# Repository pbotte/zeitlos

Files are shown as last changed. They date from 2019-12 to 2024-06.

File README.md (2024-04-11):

# Ladensystem für einen automatischen Dorfladen

Ein Paket aus Soft- und Hardware für ein automatisches Ladensystem, welches sich für kleine Läden, bis ca. 1000 Produkte, eignet. Das System basiert darauf, dass jedes Produkt durch eine eigene Waage gewogen wird, welche mit einem Computer verbunden ist.

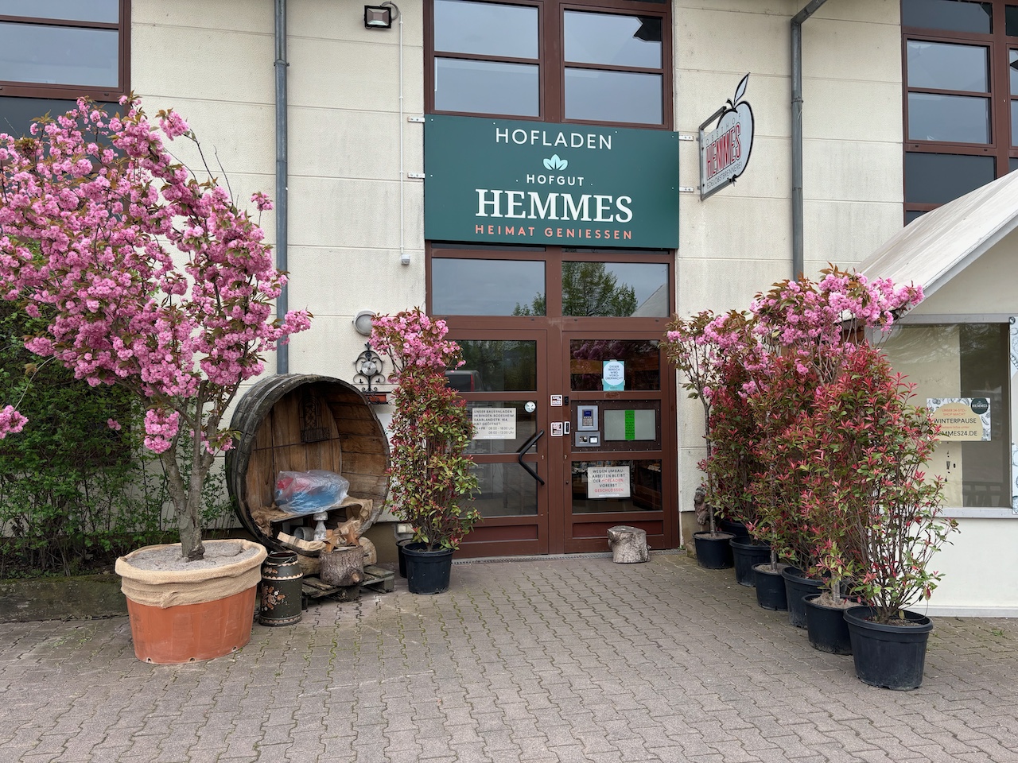
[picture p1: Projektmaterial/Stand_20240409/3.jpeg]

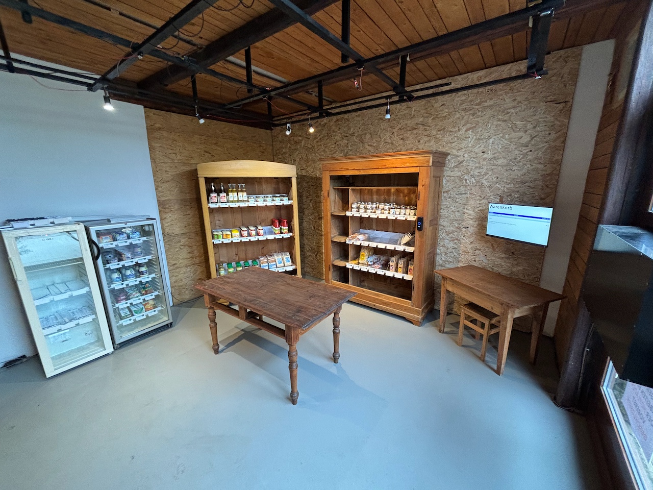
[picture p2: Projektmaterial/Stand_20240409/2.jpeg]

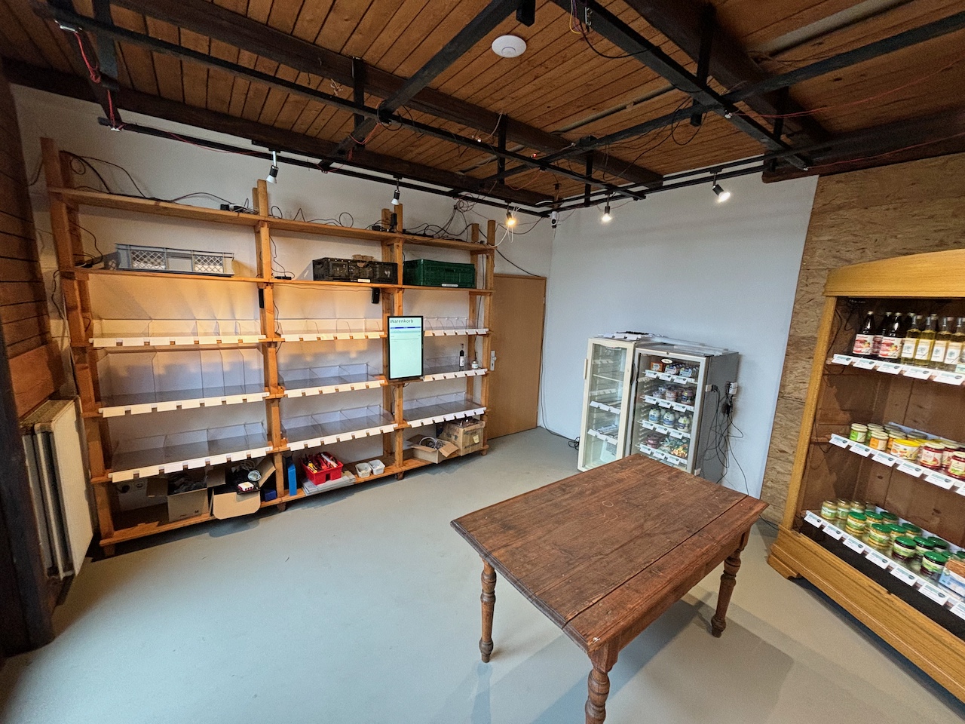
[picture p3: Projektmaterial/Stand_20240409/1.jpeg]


## Beschreibung eines typischen Einkaufs:
1. Einlass mit Girocard oder Kreditkarte. Dabei findet eine Vorauthorisierung (Reservierung von Geld) statt.
2. Der Kunde betritt den Laden und entnimmt die Waren selbst aus den Regalen. Die Anzeige der entnommen Waren und Massen erfolgt sofort und automatisch auf den Kundendisplays.
3. Zum Abschluss des Einkaufs verlässt der Kunde den Laden. Die Abrechnung erfolgt anschließend automatisch über die Karte ohne dass die Karte erneut vorgezeigt werden muss.

Es kann immer nur ein Kunde gleichzeitig einkaufen.

## Hinweise
* [Kostenübersicht](kostenuebersicht.md)

## Technische Details 
* [Zustände eines Einkaufs](ablauf.md)
* [Bestandteile des Ladens / MQTT-Übersicht](MQTT_Overview.md)
* In den jeweiligen Unterordnern gibt es weitere Markdown-Dateien mit Erläuterungen zur Installation und Befehlen.
* Zum gleichzeitigen Herunterladen der Submodule: 
  ```bash
  git clone --recurse-submodules  git@github.com:pbotte/zeitlos.git
  ```

## Lizenz
Alle Soft- und Hardware stehen unter der [GPL v3](https://github.com/pbotte/zeitlos/blob/master/LICENSE) zur freien Verfügung.

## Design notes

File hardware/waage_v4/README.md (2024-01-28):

# Waage V4

* Waage aus 3D Drucker
* Wiegen mit 4 Wägezellen, Halbbrücke
* Kosten: 25€/Waage mit Druck und Elektornik, ohne Montage.
* Stand: Fertig entwickelt.

## 3D-Daten: 

[Modell hier herunterladen](https://cad.onshape.com/documents/e93dca015aaa1e9e19b301b1/w/7b48b7bfd47193fa3707ac4f/e/e2c3e895b10e82bbda4e5613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
) und ausdrucken via
* 3D FDM Drucker, oder
* https://craftcloud3d.com

## Elektronik-Platine:
* [Schematics](elektronik/illustrative/schematics.pdf)

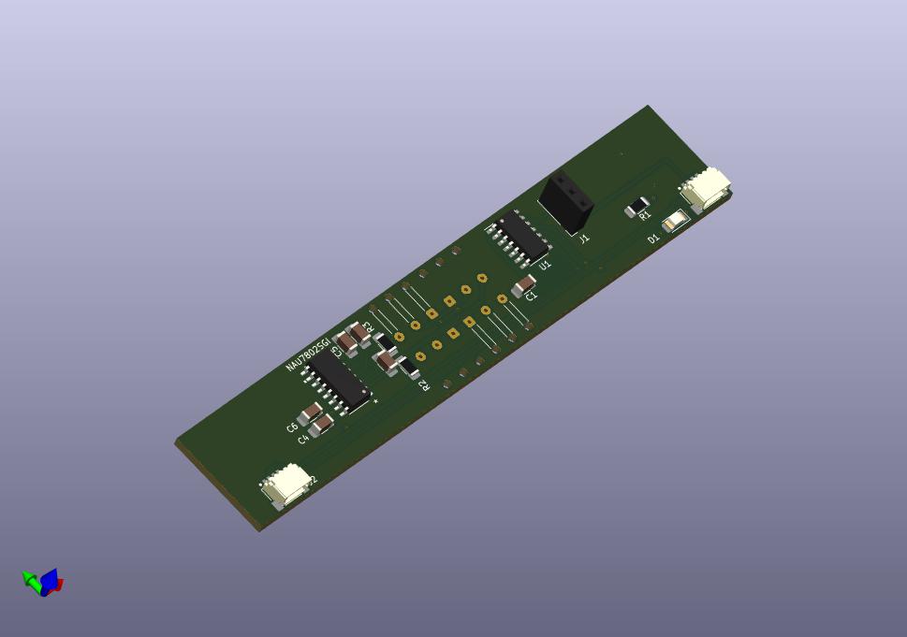
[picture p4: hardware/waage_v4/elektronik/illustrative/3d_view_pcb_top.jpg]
Top

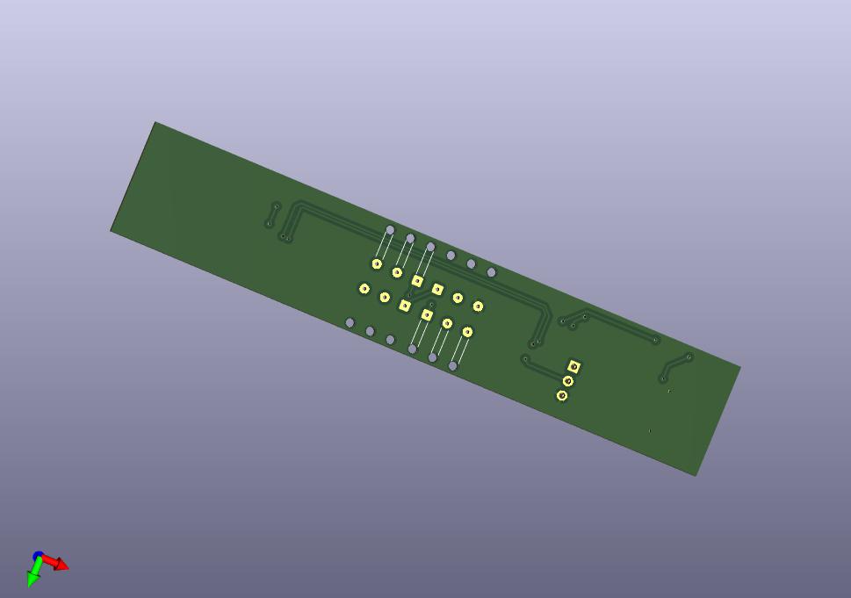
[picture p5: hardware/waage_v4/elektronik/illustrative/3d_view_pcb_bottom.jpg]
Bottom


## Materialien:
* Anschlusskabel: 
  * 50mm
  * https://www.mouser.de/ProductDetail/485-4399
* 4er Set Wägezellen:
  * Halbbrücken
  * 40cm Kabel
  * 1kOhm
  * https://www.aliexpress.com/item/1005004455387340.html
* Acrylglas Rundstab 2mm
  * klar, als Lichtleiter eingesetzt
  * https://hbholzmaus.de/epages/Store7_Shop34800.sf/de_DE/?ObjectPath=/Shops/Shop34800/Products/%2200-Ø2-00%22/SubProducts/%2200-Ø2-2000%22

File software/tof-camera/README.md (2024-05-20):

# Ausführung

```bash
pip install --break-system-packages -r requirements.txt

python3 ./software/roy-tof-camera/libroyale-5.10.0.2751-LINUX-arm-64Bit/python/tof_camera_readout.py -v -b 192.168.10.10
```

# Vobereitung

### Hardware:
- Raspi 4B, 1GB
- Raspbian, 64bit, Desktop

### Erster Test, ob Kamera korrekt angeschlossen:

```bash
cd Desktop/libroyale-5.10.0.2751-LINUX-arm-64Bit/bin/
sudo ./royaleviewer 
```

### udev-rules installieren, damit ohne sudo ausführbar
```bash
cd Desktop/libroyale-5.10.0.2751-LINUX-arm-64Bit/driver/udev/
sudo cp 10-royale-ubuntu.rules /etc/udev/rules.d/
```

### System vorbereiten
Anleitung: https://www.youtube.com/watch?v=8IJLDIYbaCg&t=156s
```bash
cd Desktop/libroyale-5.10.0.2751-LINUX-arm-64Bit/python/
sudo apt update
sudo apt upgrade
sudo apt install libusb-1.0-0 qtbase5-dev libopengl0 python3 python3-tk python3-matplotlib python3-numpy cmake cmake-gui swig
sudo reboot
````

Warpper für aktuelles python installieren
```bash
cd Desktop/libroyale-5.10.0.2751-LINUX-arm-64Bit/python/
cat README.md 

#noch eine Datei reinkopieren:
# von hier: https://github.com/numpy/numpy/tree/master/tools/swig
cd swig
wget https://raw.githubusercontent.com/numpy/numpy/main/tools/swig/numpy.i

#cmake-gui braucht das aktuelle Verzeichnis der libpython, dies ggf. mit find zuvor suchen
PYTHON_LIBRARY=/usr/lib/aarch64-linux-gnu/libpython3.11.so cmake-gui 

#Vorgehen / dort auswählen:
# - Eingabe-Pfad: python/swig Verzeichnis
# - Ausgabe neuen Ordner: python/build
# Configure, dort 2. Eintrag in Dropdown auswählen: "UNIX..."
# Haken bei cmake option für numpy.i anwählen
# Generate klicken
# cmake-gui verlassen

#build script ausführen
cd python/build/
make

#erzeugte Datei nach python kopieren
cd python/
mv _roypy.so _roypy.so-3.8
cp build/_roypy.so .
```
### Beispiel ausprobieren
```bash
python3 ./sample_retrieve_data.py 
````

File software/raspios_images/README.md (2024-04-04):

# Installation eines Computers

## Quick and easy:

1) Use [Raspberry Pi Imager](https://www.raspberrypi.com/software/), copy lite or standard image to SD card. Activate SSH server, set hostname (eg `shelf01`) and password for user `pi`. Check the right localisation options. Press `CTRL + SHIFT + X` in the imager to reach the advanced options.

   ALTERNATIVELY: Hold down the `shift`-key while powering up the raspberry and install the OS with the right custom settings.
2) After the first boot, run: 
   ```bash
   curl -fsSL https://raw.githubusercontent.com/pbotte/zeitlos/master/software/get.sh -o get.sh
   sudo bash get.sh
   ```
Done.

If you prefere the long way, choose this:

## The long way

Alle Opterationen in dem Verzeichnis
```bash
cd raspi_image
```

### Download des Images

Wir laden für alle Desktops to Version mit Desktop von der [offiziellen Seite](https://www.raspberrypi.com/software/operating-systems/), um später leichter einen Browser anzeigen zu können. Später wird lediglich entschieden, bis wohin gebootet werden soll (Console oder Desktop)

```bash
wget https://downloads.raspberrypi.com/raspios_armhf/images/raspios_armhf-2023-12-06/2023-12-05-raspios-bookworm-armhf.img.xz
```

### Image und Dateien kopieren

Nachschauen, wo es hingehen soll
```bash
lsblk
#macos
diskutil list
```

Dann kopieren:
```bash
xzcat 2023-12-11-raspios-bookworm-armhf-lite.img.xz | sudo dd of=/dev/sdc bs=1M status=progress conv=fsync

# unter macos 
# use devices with additional "r" eg /dev/rdisk2)
diskutil unmountDisk /dev/disk2
xzcat 2023-12-05-raspios-bookworm-armhf.img.xz | sudo dd of=/dev/rdisk2 bs=1m status=progress conv=sync
```

Alternativ mit separatem Decompress, falls es nicht funktioniert (Das Schreiben hört hie auf...)
```bash
xz -d -v 2023-12-05-raspios-bookworm-armhf.img.xz 
sudo dd if=2023-12-05-raspios-bookworm-armhf.img of=/dev/rdisk2 bs=1m status=progress conv=sync
```

Vorbereiten für das Kopieren der Konfigurationsdateien:
```bash 
mount /dev/sdc1 boot/ 
cp firstrun.sh ./boot/ # macos: Volumes/bootfs 

#entweder die komplette Datei kopieren oder die wichtigen Zeichen in cmdline.txt einfügen
cp cmdline.txt ./boot/ # macos: Volumes/bootfs 
```

Die wichtigen Zeichen in `cmdline.txt` sind:
```
systemd.run=/boot/firstrun.sh systemd.run_success_action=reboot systemd.unit=kernel-command-line.target
```
(Alles in einer Zeile!)

Für Lite-OS in Gänze:
```bash
console=serial0,115200 console=tty1 root=PARTUUID=57c84f67-02 rootfstype=ext4 fsck.repair=yes rootwait quiet init=/usr/lib/raspberrypi-sys-mods/firstboot systemd.run=/boot/firstrun.sh systemd.run_success_action=reboot systemd.unit=kernel-command-line.target ipv6.disable=1
```

### Browser Kiosk Modus

#### Neu, Seit Wayland, ca. 2024

Anleitung: https://www.raspberrypi.com/tutorials/how-to-use-a-raspberry-pi-in-kiosk-mode/

Zusammengefasst: `wtype` installieren und die Datei `wayfire.ini` ergänzen. Im Text den `hostname` anpassen.
```bash
sudo apt install wtype
sudo nano .config/wayfire.ini

[autostart]
panel = wfrespawn wf-panel-pi
background = wfrespawn pcmanfm --desktop --profile LXDE-pi
xdg-autostart = lxsession-xdg-autostart
chromium = chromium-browser http://shop-master/?hostname=shop-display02 --kiosk --noerrdialogs --disable-infobars --no-first-run --ozone-platform=wayland --enable-features=OverlayScrollbar --start-maximized
screensaver = false
dpms = false
```

### Auswerfen 
```bash 
umount ./boot/
#unter mac os
sudo diskutil eject /dev/rdisk2
```

### Hinweise

#### Hinweis 1
Nicht alles was mit raspi-config geht ist [offiziell](https://www.raspberrypi.com/documentation/computers/configuration.html#list-of-options30) dokumentiert. Alternativ den Quellcode nach Befehlen suchen mit:
```bash
curl -sL https://github.com/RPi-Distro/raspi-config/raw/master/raspi-config | grep -E '(do|get)_[a-zA-Z0-9_ ]+\(' | sort | uniq
```
(Tipps von [hier](https://raspberrypi.stackexchange.com/questions/28907/how-could-one-automate-the-raspbian-raspi-config-setup))

#### Hinweis 2

Ein Skript, welches per `systemd.run=/boot/firstrun.sh` (?) gestartet ist, kann nicht auf das Netzwerk zugreifen. Kann man machen, was man will (inkl. Workaround):

https://unix.stackexchange.com/questions/686612/wait-for-network-on-systemd-run-kernel-parameter-like-require-wants-in-systemd

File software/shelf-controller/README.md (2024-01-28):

# Shelf Controller I2C

- MQTT-Client name: `shelf01`, etc.
- MQTT-topic-prefix: `homie/shelf01`
- MAC-Adresse von Scale (6x byte): `aabbccddeeff`
- EEPROM Adressnuztung: 0: I2C Adresse, 1..4: Steigung (4bytes float), 5..8: Nullwert (4bytes float)

| R/W | MQTT Topic <br> (ohne Topic-prefix) | Retain | Typischer Wert | Aktion |
| --- | --- |:---:| --- | --- |
| W | `/state` | X | `0` oder `1` | online / offline, per Last-Will gesetzt |
| R | `/cmd/search` | | | Erneut nach Waagen suchen |
| R | `/cmd/leds` | | `0`oder `1` | Setze alle LEDs am Bus an/aus |
| R | `/cmd/restart` | | egal | Starte alle Waagen am Bus neu. Warte 8 Sekunden, bis dies sicher durchgeführt ist. |
| R | `/cmd/set_zero` | | egal | Setze den aktuellen Mittelwert als `scale_calibration_zero_in_raw` |
| R | `/cmd/scales/aabbccddeeff/set_slope` | | `0.001`..`200` (in kg) | Setze die Steiung zur Kalibration. (Messwert-`scale_calibration_zero_in_raw`)*Steigung = Wert in kg |
| R | `/cmd/scales/aabbccddeeff/led` |  | `0` oder `1` | Schalte individuelle LED ein/aus |
| W | `/scales/aabbccddeeff/state` | X | `0` oder `1` | online / offline (sollte jedoch `/state==0` sein, dann gelten diese Werte nur als historisch) |
| W | `/scales/aabbccddeeff`<br>`/firmware_version` | X | `uint`  | Wird von der Waage ausgelesen |
| W | `/scales/aabbccddeeff`<br>`/hardware_version` | X | `uint`  | Wird von der Waage ausgelesen |
| W | `/scales/aabbccddeeff`<br>`/scale_calibration_zero_in_raw` | X | `32-bit uint`  | Waagen-Kalibration Roh-ADC-Wert bei 0kg auf Waage |
| W | `/scales/aabbccddeeff`<br>`/scale_calibration_slope` | X | `double` | Waagen-Kalibration, Steigung nach Abzug des Roh-0kg-Werts, Ergebnis: kg |
| W | `/scales/aabbccddeeff`<br>`/i2c_address` | X | `9..117` (byte)  | I2C-Adresse der Waage, nur zur Info |
| W | `/scales/aabbccddeeff`<br>`/raw` | | `32-bit uint` | Roh-Messwert des ADCs (nur im Modus `-vv`) |
| W | `/scales/aabbccddeeff`<br>`/mass` | | Wert in kg, double | Aktuelle Masse unter Anwendung der Kalibration ggf. unter Berücksichtigung der Temperatur |
| W | `/scales/aabbccddeeff`<br>`/touched` | | `0`oder `1` | Wenn die Waage zuletzt mit dem Finger belastet wurde ODER eine Laständerung eintrat, dann soll hier eine `1` übermittelt werden. |

## Start von shelf-controller
```mermaid
sequenceDiagram
    actor Techniker
    participant shop-controller
    participant shelf-controller
    participant Waage
    Techniker->>shop-controller: Startet Programm
    shop-controller->>shop-controller: schreibt: shop_overview/products
    shop-controller->>shop-controller: schreibt: shop_overview/products_scales
    Techniker->>shelf-controller: Startet Programm,<br>liest /products und /products_scales<br>(und hält aktuell)
    shelf-controller->>Waage: Sucht nach Waagen
    Waage->>shelf-controller: Meldet sich zurück
    shelf-controller->>Waage: Fragt Waage nach Roh-Wert
    Waage->>shelf-controller: Gibt Roh-ADC-Messwert
    shelf-controller->>shelf-controller: Wendet Kalibrierung von calib/scale-aabbccddeeff an 
```

## Beispiele

| Topic | Wert | 
| --- | --- |
| `homie/shop_controller/shop_overview/products` | `{"1": {"ProductID": 1, "ProductName": "Kuerbis", "ProductDescription": "eigene Ernte", "PriceType": 0, "PricePerUnit": 4.0, "kgPerUnit": 1.67}, "2": {"ProductID": 2, "ProductName": "Nudeln", "ProductDescription": "Hausgemacht mit frischen Eiern", "PriceType": 0, "PricePerUnit": 2.6, "kgPerUnit": 0.5}, "3": {"ProductID": 3, "ProductName": "Cocktailtomaten", "ProductDescription": null, "PriceType": 0, "PricePerUnit": 4.45, "kgPerUnit": 0.5}, "4": {"ProductID": 4, "ProductName": "Tomaten", "ProductDescription": null, "PriceType": 0, "PricePerUnit": 2.15, "kgPerUnit": 0.6}, "5": {"ProductID": 5, "ProductName": "Eier L 10er", "ProductDescription": "aus Bodenhaltung", "PriceType": 0, "PricePerUnit": 3.3, "kgPerUnit": 0.6}, "6": {"ProductID": 6, "ProductName": "Weizenmehl", "ProductDescription": "1kg Type 550", "PriceType": 0, "PricePerUnit": 1.59, "kgPerUnit": 1.04}, "7": {"ProductID": 7, "ProductName": "Gummibaerchen", "ProductDescription": null, "PriceType": 0, "PricePerUnit": 1.9, "kgPerUnit": 0.155}, "8": {"ProductID": 8, "ProductName": "Haltbare Milch", "ProductDescription": "1L im Tetrapack", "PriceType": 0, "PricePerUnit": 1.69, "kgPerUnit": 1.1}, "9": {"ProductID": 9, "ProductName": "Birnen", "ProductDescription": "750g Eigene Ernte Alexander Lukas", "PriceType": 0, "PricePerUnit": 1.0, "kgPerUnit": 0.775}}}` |
| `homie/shop_controller/shop_overview/products_scales` | `{"shelf01/b963": 1, "shelf01/ca44": 2, "shelf01/d660": 5, "shelf01/3320": 6, "shelf01/1a6d": 7, "shelf01/1503": 8, "shelf01/12d4": 12, "shelf01/73d0": 17, "shelf01/95e": 18, "shelf01/2438": 19, "shelf01/84a7": 20, "shelf01/65c0": 21, "shelf01/7b87": 22, "shelf01/7e3e": 23}`

# Automatischer Start und Terminierung des Controllers

Dies geschieht mittels udev und systemd über die beiden Dateien `99-runScales.rules` und `scale@.service`. Durch die Konfiguration in der systemd-Datei ist sichergestellt, dass das Programm erst dann gestartet wird, wenn der serielle Anschluss bereit ist (After=) und beendet wird, sobald dieser verschwindet (BindTo=).

## Installationsanleitung

Nach einem git clone des Repositories müssen die beiden Dateien in die richtigen Systemverzeichnisse kopiert werden:

```bash
sudo cp zeitlos/software/shelf-controller/99-runScales.rules /etc/udev/rules.d/
sudo cp zeitlos/software/shelf-controller/scale@.service /etc/systemd/system/
```
Anschließend noch die Änderungen an Systemd mitteilen mittels:
```bash
sudo systemctl daemon-reload
```
Wird nun ein Scale Controller an den Computer angesteckt, so wird automatisch der Scale Controller gestartet. Wird er entfernt, so beendet sich dieser auch wieder.

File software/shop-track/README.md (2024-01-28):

# Automatischer Start und Terminierung des Controllers

Dies geschieht mittels udev und systemd über die beiden Dateien `99-runShopTrack.rules` und `shop-track@.service`. Durch die Konfiguration in der systemd-Datei ist sichergestellt, dass das Programm erst dann gestartet wird, wenn der serielle Anschluss bereit ist (After=) und beendet wird, sobald dieser verschwindet (BindTo=).

## Installationsanleitung

Nach einem git clone des Repositories müssen die beiden Dateien in die richtigen Systemverzeichnisse kopiert werden:

```bash
sudo cp zeitlos/scaleController/99-runShopTrack.rules /etc/udev/rules.d/
sudo cp zeitlos/scaleController/shop-track@.service /etc/systemd/system/
```
Anschließend noch die Änderungen an Systemd mitteilen mittels:
```bash
sudo systemctl daemon-reload
```
Wird nun ein Raspberry Pico an den Computer angesteckt, so wird automatisch der Shop-Track Controller gestartet. Wird er entfernt, so beendet sich auch der Scale-Track Controller.

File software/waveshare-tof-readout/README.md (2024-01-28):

# Installation Variante 1

Die Datei `shop-track00.service` als Vorlage nehmen und mit dem `/dev/serial/by-path/...` füllen.

```bash
sudo cp shop-track00.service /etc/systemd/system/
```

Dies für jeden angeschlossen Serial-Converter wiederholen und die Ziffern hochzählen.

# Installation Variante 2

## Automatischer Start und Terminierung des Controllers

Dies geschieht mittels udev und systemd über die beiden Dateien `99-runTracker.rules` und `tracker@.service`. Durch die Konfiguration in der systemd-Datei ist sichergestellt, dass das Programm erst dann gestartet wird, wenn der serielle Anschluss bereit ist (After=) und beendet wird, sobald dieser verschwindet (BindTo=).

## Installationsanleitung

Nach einem git clone des Repositories müssen die beiden Dateien in die richtigen Systemverzeichnisse kopiert werden:

```bash
sudo cp zeitlos/software/waveshare-tof-readout/99-runTracker.rules /etc/udev/rules.d/
sudo cp zeitlos/software/waveshare-tof-readout/tracker@.service /etc/systemd/system/
```
Anschließend noch die Änderungen an Systemd mitteilen mittels:
```bash
sudo systemctl daemon-reload
```
Wird nun ein Serial Converter an den Computer angesteckt, so wird automatisch das Prorgamm gestartet. Wird er entfernt, so beendet sich dieses auch wieder.

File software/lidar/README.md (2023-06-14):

# Installationshinweise

## lidar-readout 

Service auf dem Raspi, an dem der Lidar via USB angeschlossen ist, welcher nur die Daten ausliest und 
anschließend per MQTT versendet.

Vor dem Laden Betreten soll immer eine Referenz-Messung durchgeführt werden (Temperatur unterschiede, Wackler bei Anbringung etc., Rumstehende Dinge). 

## lidar-control

Service auf dem zentralen Computer, welcher die Daten von ggf. mehreren lidar-readouts entgegenimmt und 
eine eine zentrale Aussage über die Belegung des Ladens erzeugt. Gibt auch die Befehle über an/aus an
die einzelnen Lidars weiter.

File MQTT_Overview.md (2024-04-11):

```mermaid
graph TD
  W1["Waagen 1..N"] <--> |I2C| WC1
  W2["Waagen 1..N"] <--> |I2C| WC2
  W3["Waagen 1..N"] <--> |I2C| WCN

  WC1["shelf-controller.py 1"] ==> |Messwerte| SC
  WC2["shelf-controller.py 2"] ==> |Messwerte| SC
  WCN["shelf-controller.py N"] ==> |Messwerte| SC

  L1["Lidar 1..4"] --> |Serial| ST1
  L2["Lidar 1..4"] --> |Serial| ST2
  LN["Lidar 1..4"] --> |Serial| STN

  ST1["Lidar Readout 1"] ==> |Rohdaten| STI
  ST2["Lidar Readout 2"] ==> |Rohdaten| STI
  STN["Lidar Readout N"] ==> |Rohdaten| STI

  Türkontakt --> |Klingeldraht| IOR

  SC["Shop controller"]

subgraph Messdaten-Input
  WC1
  WC2
  WCN
  cardreader
  STI["shop-track-collector.py"]
  IOR["io-usb-readout"]
end

subgraph Ausgabe
  FSR["FSR14Control"]
  DPC["display-power-control"]

  MN["mqtt-2-ntfy"]

  Shelly["Shelly Rollladen-Controller"]

  UW["Update Public Webpage"]
end

  SC ==> Shelly --> Rollladen
 
  IOR ==> |offen/zu| SC

  DPC --> CD1
  DPC --> CD2
  DPC --> CDA

  CD1["Client Live Display 1"]
  CD2["Client Live Display 2"]
  CDA["Client Display Außen"]

  FSR --> LI["Licht innen"]
  FSR --> LA["Licht außen"]
  FSR --> Türöffner

  STI ==> |Kunde im Laden?| SC
  cardreader <==> SC

  SC ==> FSR
  SC ==> DPC

  SC ==> MN

  SC ==> UW

  NR["NodeRed"] <==> SC
```

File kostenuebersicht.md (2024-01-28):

# Kostenübersicht

Alle Preise inkl. MwSt. Stand: 9.1.2023

## Präsenzsystem
Zur Bestimmung, ob Personen im Laden vorhanden. Bezählt wird nur die begehbare Ladenfläche ohne Stellfläche für Regale.

Pro m^2 Ladenfläche, je 1x:
- [Waveshare 18301 TOF Laser Entfernungsmesser](https://www.welectron.com/Waveshare-18301-TOF-Laser-Range-Sensor) 25€
- Verbindungskabel 1m, [kundenspezifische Anfertigung Alibaba](https://hshytech.en.alibaba.com/), 1,20€/Stück
- Halterung aus Plastik, 3D-Druck, Materialkosten: 0,25€
- 2 Schrauben M3x8mm
- 2 Holz-Schrauben 3x18

Pro 8m^2 Ladenfläche:
- [Serial to USB-Konverter 3,3V](https://www.berrybase.de/konverter-micro-usb-buchse-uart-pl2303) 3,90€
- USB-Kabel 2€

Falls mehr als 4 USB-Konverter: USB-Hub für 20€

Für die Auslese:
- [Raspberry Pi 4 1GB](https://www.berrybase.de/raspberry-pi-4-computer-modell-b-1gb-ram?c=319) (39,90€)
- [microSD Speicherkarte High Endurance](https://www.berrybase.de/sandisk-high-endurance-microsdhc-uhs-i-u3-speicherkarte-adapter-32gb) 9,30€
- [Raspberry USB-Netzteil](https://www.berrybase.de/offizielles-raspberry-pi-usb-c-netzteil-5-1v/3-0a-eu-schwarz) 7,90€
- [Gehäuse](https://www.berrybase.de/offizielles-gehaeuse-fuer-raspberry-pi-4-schwarz/grau) 4,90€
- [Netzwerkkabel 10m](https://www.berrybase.de/cat-6-netzwerkkabel-s/ftp-ls0h-weiss?number=93503&c=277) 6,50€ 

### Summe
Bei 16m^2: 515€

## Waagen

Pro Waage, 125mm Breite:
- [Alu-Metallplatte mit Laser-Schnitt, 379x122x2,5mm](https://laserteileonline.de/laserteile-konfigurator/): 6,73€
- [4x Wägezelle](https://de.aliexpress.com/item/1005004455387340.html): 2,46€
- Plastikunterteil, ca. 8€
- [Produkttrenner, Rechteckig, 2mm PETG:](https://kunststoffplattenprofis.de/produkt/pet-g-farblos/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): 1,50€
- T-Stück zum Halten des Produkttrenners, 3D-Druck, 0,06€
- Rückwand: (anteilig) 0,74€
- [Metall-Viereckstab vorne](https://alu-spezi.de/epages/39916185-3f40-410c-8304-8e98310e5b8d.sf/de_DE/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): (anteilig) 0,50€
- Preisschild, 3D-Druck: 0,36€
- Elektronik, JLCPCB: 4,50€
- [Qwiic-Verbindungskabel](https://www.mouser.de/ProductDetail/485-4399): 1,05€
- [Acrylglas-Stab für Lichtleiter](https://hbholzmaus.de/epages/Store7_Shop34800.sf/de_DE/?ObjectPath=/Shops/Shop34800/Products/%2200-Ø2-00%22/SubProducts/%2200-Ø2-2000%22): (anteilig) 0,5€

### Summe
26,40€ pro Waage

Bei 200 Waagen: 5280€

Anmerkung: Zusammenbau und Anlöten der Wägezellen fehlt.

## Waagenauslese

Pro Regalebene (1-20 Waagen):
- Ausleseelektronik, JLCPCB: 7€
- QWIIC-Kabel 50cm: 3€
- USB-Kabel: 2€

Pro 7 Auslese-Elektroniken:
- USB-Hub: 20€
- Auslese-Computer: Raspberry Pi, 1GB (+ Zubehör): 62€
- Netzwerkkabel 10m: 6,50€

### Summe

Typisch sind 25 Auslesen, 3 Hubs und 3 Computer: 565 €

## Kundenanzeige

- 24" HDMI-Monitor: 130€
- HDMI-Kabel (HDMI auf Mini-HDMI): 5€
- Raspberry PI mit 2GB (+ SD-Karte, Netzteil, Gehäuse): 72€
- Netzwerkkabel 10m: 6,50€
- Monitorhalterung: 30€

### Summe

Pro Anzeige: 244€

## Kartenlesegerät 

- OPP C60 für 1600€ (plus MwSt.)
- Halterungen, 3D gedruckt, mit Gewindeeinsätzen: 10€

## Überwachungssystem

- Dreammachine Pro: 520€
- Festplatte: 100€
- 3x Kamera G3 flex plus Netzwerkkabel: 80€+10€
- Netzwerkschrank: 80€
- WLAN AP: 100€
- Türklingel G4 WLAN außen: 190€
- Türklingel Ge PoE innen + Türgong: 420€

### Summe
1680€

## Türzugang und Beleuchtungssteuerung

- Elektroschrank mit Türe: 50€
- Raspberry Pi (+ SD-Karte, Netzteil, Gehäuse): 72€
- USB-RS485-Konverter: 15€
- Eltako FSR14-4x: 45€
- Eltako: FBA14: 23€
- Netzteil für Relais, 12V: 30€
- 12V Netzteil für Magnetschalter Türe: 15€
- Magnetschalter Türe: 20€
- Magnet-Türkontakt: 10€
- Kabel: 230V und Steuerkabel Türe

### Summe
280€

## Kontrollrechner

Kontrolliert den ganzen Laden:
- Raspberry 4GB (+ SD-Karte, Gehäuse, Netzteil): 92€
- Netzwerkkabel 1m: 1,50€

## Globale Summe

Für ein System mit 200 Waagen und 16m^2 begehbare Ladenfläche.

| Teilsystem | Kosten in € |
|---| ---:|
| Präsenzsystem für 16m^2 |  515|
| 200x Waagen | 5.280 |
| 25x Waagenauslese | 565 |
| 3x Kundenanzeige | 732 |
| Kartenlesegerät | 1.600 |
| Kameraüberwachung | 1.680 |
| Türzugang und Beleuchtungssteuerung | 280 |
| Kontrollrechner | 93 |
| **Summe** | 10.745  |

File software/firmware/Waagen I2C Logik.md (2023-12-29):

# Waagen I2C 

- Der Master fragt regelmäßig alle Waagen ab, so schnell er kann. 
- Die LED wird bei Bedarf geändert. 
- Master kann einen Busscan durchführen um den Waagen eine neue eindeutige I2C Adresse zu geben.

## Generelle Logik

- Daten in EEPROM:
  - EEPROM, byte 0: I2C-Adresse (7bit)
  - EEPROM, bytes 1..4: 4bytes float Steigung
  - EEPROM, bytes 5..8: 4bytes float Waagen-Nullwert

- Alle Waagen haben eine 6x 8bit MAC-Adresse. Sie wird aus der Chip Seriennummer abgeleitet.

- I2C Bus-Geschwindigkeit: sollte so niedrig sein, dass er auch als "Feldbus" über die langen Distanzen funktionieren kann. 
  - Evtl. die Widerstände niedriger wählen, siehe auch https://www.nxp.com/docs/en/application-note/AN10216.pdf Slide 41 auf Seite 17. 
  - 1,3kOhm ist die statische untere Grenze, daneben gibt es noch eine dynamisch (rise time).

Alle Waagen hören lesend auf:
- Adresse `0x00` (Broadcast/"General Call", https://www.i2c-bus.org/addressing/general-call-address/, nur schreibend möglich, kein Lesen von target)
- schreibend auf `0x08` (erste freie Adresse nach den reservierten Bereich `0..7`) und 
- r/w auf ihrer individuellen Adressen `9..119`:

| I2C Adr. | Richtung | Byte 0 = cmd | Anz. Bytes <br>(excl. cmd byte) | Erläuterung |
| --- | -- | -- | -- | -- |
| `0x00` | w | `0x00` | 0 | Alle Waagen: Neustart  |
| `0x00` | w | `0x01` | 0 | Alle Waagen: Antwort-Bit zurücksetzen |
| `0x00` | w | `0x02` | 7 | I2C-Adresse setzen, MAC(Bytes 1..6), I2C-Adresse(Byte 7)  |
| `0x00` | w | `0x03` | 6 | Setzen der Referenz-MAC-Adresse, vgl. auch Read von Adresse `0x8` |
| `0x00` | w | `0x04` | 0 | LEDs aller Waagen: aus |
| `0x00` | w | `0x05` | 0 | LEDs aller Waagen: ein |
| `0x08` | r | - | 1 | Rückmeldung ob MAC-Adresse kleiner gleich der gesuchten. |
| `9..119` | r | - | <br>4 ODER<br>13 ODER<br>11 ODER<br>1 | Abhängig von Register: vgl. write `0x00`/`0x01`/`0x04`/`0x06` an `9..119`<br>Waagenwert (Byte 0..3) ODER<br>MAC-Adresse (Byte 0..5) und LED-Status (Byte 6) und BUILD_NUMBER (Byte 7..10) und Hardware_Revision (Byte 11..12) ODER <br>Ergebnis des Selbsttests ODER<br>EEPROM data (single byte) from selected address |
| `9..119` | w | `0x00` | 0 | nächtes Lesen enthält Waagen-Wert |
| `9..119` | w | `0x01` | 0 | nächtes Lesen enthält MAC-Adresse und LED-Status und BUILD_NUMBER und Hardware_Rev |
| `9..119` | w | `0x02` | 0 | LED aus |
| `9..119` | w | `0x03` | 0 | LED an |
| `9..119` | w | `0x04` | 0 | Start Chip Self Test (read result in next step) |
| `9..119` | w | `0x05` | 2 | Write to EEPROM. 1st byte = address, 2nd byte = data byte |
| `9..119` | w | `0x06` | 1 | Prepare read from EEPROM. 1st byte = address. After this command, read one byte from `9..119` |

## Einschalten der Waagen

- Beim Einsetzen der Stromversorgung nimmt die Waage die I2C-Adresse, welche sie bereits zuvor hatte, aus dem EEPROM. 
- Dies dient der Vermeidung von fehlenden Adressen bei  einer wackeligen Stromverbindung oder Stcker-Wackelkontakt.

- Stromversorgung des I2C-Bus sollte via MOSFET durch I2C Master steuerbar sein. Alternativ: USB-Hub mit Power Switch functionality.

## Setzen der I2C-Adressen / Suchen von Waagen

1. Master sendet auf Adresse `0x0` und Daten `0x1`: Alle Waagen setzen ihr Antwort-Bit zurück.
2. Master sendet auf Adresse `0x0` und Daten `0x03`+`0xxx xx xx xx xx xx` (7 bytes): MAC-Adresse, welche bei der nächsten Abfrage als Referenz gilt.
3. Master fragt ab, ob es ein Waage mit MAC-Adresse kleiner der Referenz gibt, die noch das Antwort-Bit gesetzt hat: Lesen eines Bytes von Adresse `0x8`.
4. Client antwortet mit 
   - `0xFF`, falls Antwort-Bit nicht mehr gesetzt ODER Adresse ist größer als Referenz
   - `0x00` (dominant bei Übertragung auf I2C-Bus), falls Adresse kleiner gleich Referenz

5. Der Master fährt so lang mit der Suche fort, bis er die MAC-Adresse einer einzelnen Waage herausgefunden hat. (Binäre Suche, suchen nach MAC-Adresse-1)
6. Der Master sendet nun an Adresse `0x0` ein "I2C Adresse setzen"-Kommando (`0x02`) mit der MAC-Adresse und der I2C-Adresse (8 Bytes).
  - Die Waage speichert sie ins EEPROM. 
  - Die Waage setzt bei sich das Antwort-Bit und antwortet damit bei zukündigen Broadcasts nur noch mit `0xFF`
  - Anschließend (`Wire.begin`) oder Neustart via `resetViaSWR()`
7. Die Suche geht so lang weiter (zurück zu Punkt 2) wie bei einem Broadcast mit der Adresse 0xFFFFFFFFFFFF noch mind. eine Waage antwortet.

ToDO: Falls die Mehrheit der Waagen mit 0xFF die eine antwortende Waage mit 0x0 elektrisch überstimmen sollte, dann muss der I2C-Bus kurzzeitig bei manchen Waagen deaktiviert und auf "z" gesetzt werden.

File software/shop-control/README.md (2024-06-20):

# Installationshinweise

Auf dem RasPi muss vor
```bash
pip install mariadb
#ggf nicht die neueste Version installieren, damit es mit den Dingen aus apt funktioniert:
pip install -Iv mariadb==1.0.7 
```

das folgende installiert werden:
```bash
sudo apt install libmariadb3 libmariadb-dev
```

## QR-Secret-Str

in die Datei `shop-controller.service` muss noch als notwendiger Parameter der QR-Secret-Str übergeben werden. Dieser muss gleich mit den auf der Webseite und php-Seiten sein.

## crontab auf shop-master

````
2 * * * * /usr/bin/timeout -s SIGINT 3610 /home/pi/.local/bin/mqtt-recorder --host localhost --mode record --file "/mnt/usbstick/mqtt-recordings/$(/usr/bin/date +"\%Y_\%m_\%dT\%H_\%M_\%S").csv"
15 3 * * * /usr/bin/find /mnt/usbstick/mqtt-recordings -type f -mtime +180 -exec rm {} \;

#Daten zur Webseite hochladen
52 * * * * /home/pi/zeitlos/software/public-www/local/sync_to_mysql.py --reset
```

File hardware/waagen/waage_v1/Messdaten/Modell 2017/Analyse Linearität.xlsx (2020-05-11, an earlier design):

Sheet: Tabelle1
 |  |  |  |  |  |  |  |  | Soll | Soll | Soll | Soll
46368 | 8451393 | 8248513 | 8528750 | 8543394 | 8451393 | 8248513 | 8528750 | 8543394 | 0 | 0 | 0 | 0 | 30.90030337 | 31.243881 | 27.54775747 | 27.02079256
46462 | 8451395 | 8248472 | 8528733 | 8543402 | 8451395 | 8248472 | 8528733 | 8543402 | 0 | 0 | 0 | 0
46556 | 8451431 | 8248517 | 8528724 | 8543430 | 8451431 | 8248517 | 8528724 | 8543430 | 0 | 0 | 0 | 0 | 0.1390513652 | 0.1405974645 | 0.1239649086 | 0.1215935665
46650 | 8451406 | 8248509 | 8528708 | 8543395 | 8451406 | 8248509 | 8528708 | 8543395 | 0 | 0 | 0 | 0 | 0.2781027303 | 0.281194929 | 0.2479298172 | 0.243187133
46744 | 8451380 | 8248503 | 8528707 | 8543371 | 8451380 | 8248503 | 8528707 | 8543371 | 0 | 0 | 0 | 0
46839 | 8451335 | 8248510 | 8528737 | 8543363 | 8451335 | 8248510 | 8528737 | 8543363 | 0 | 0 | 0 | 0
46933 | 8451340 | 8248535 | 8528798 | 8543343 | 8451340 | 8248535 | 8528798 | 8543343 | 0 | 0 | 0 | 0
47027 | 8451389 | 8248524 | 8528808 | 8543394 | 8451389 | 8248524 | 8528808 | 8543394 | 0 | 0 | 0 | 0
47121 | 8451396 | 8248471 | 8528800 | 8543358 | 8451396 | 8248471 | 8528800 | 8543358 | 0 | 0 | 0 | 0
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

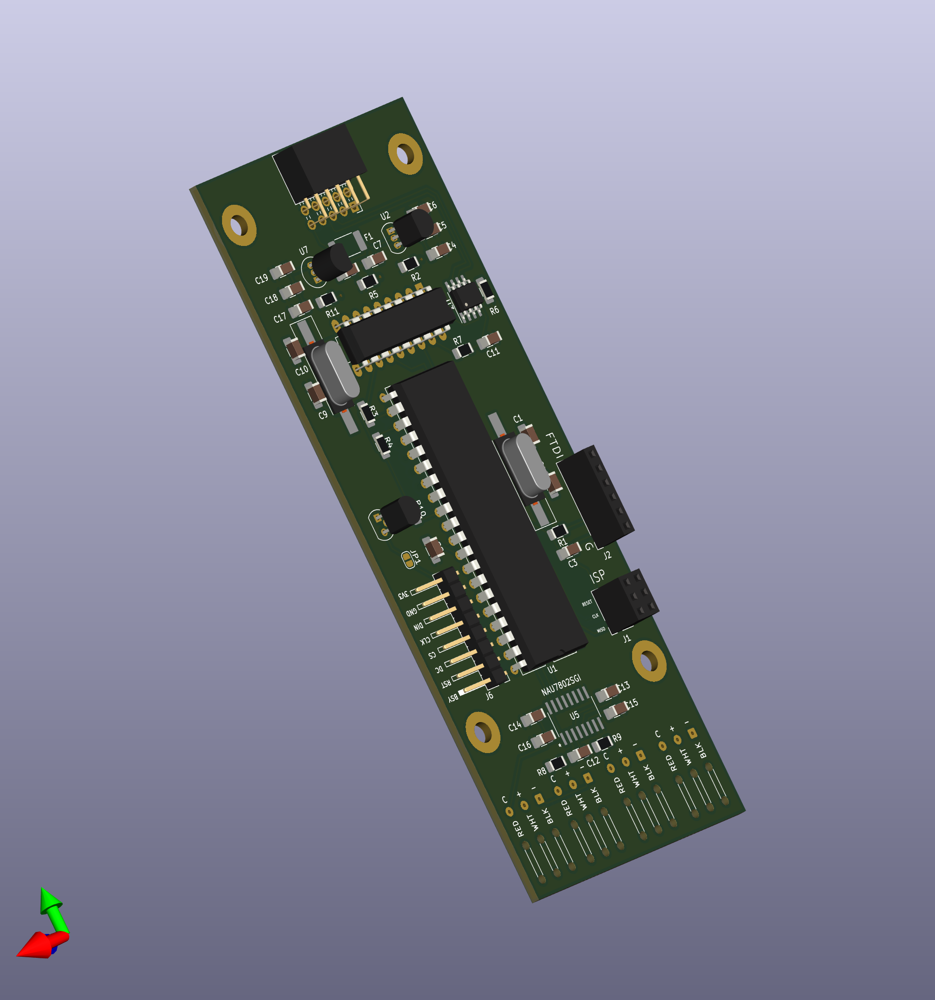
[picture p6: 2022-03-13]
hardware/waagen/waage_v2/elektronik/view-bottom.png

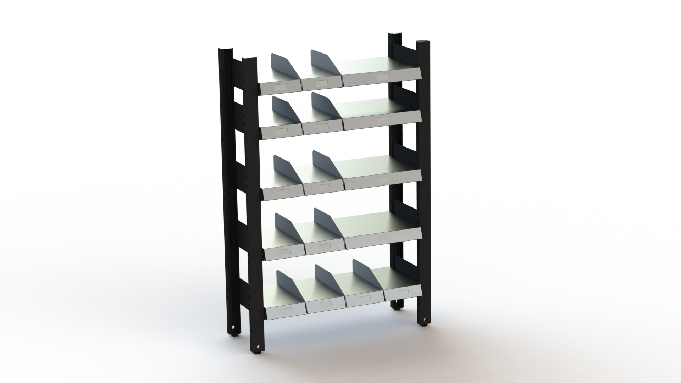
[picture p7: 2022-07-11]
hardware/regal/bilder/Regalsystem-003.JPG

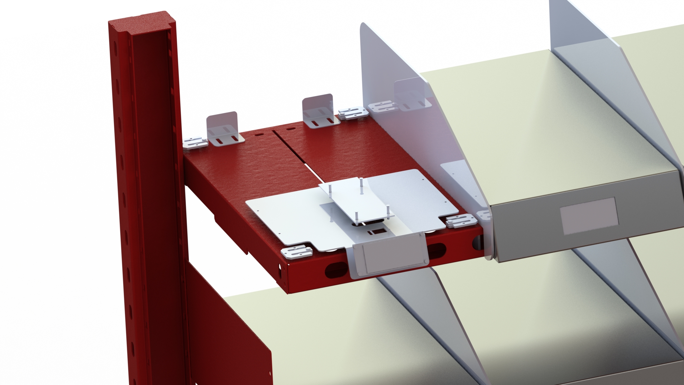
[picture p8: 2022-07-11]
hardware/regal/bilder/Regalsystem-005.JPG

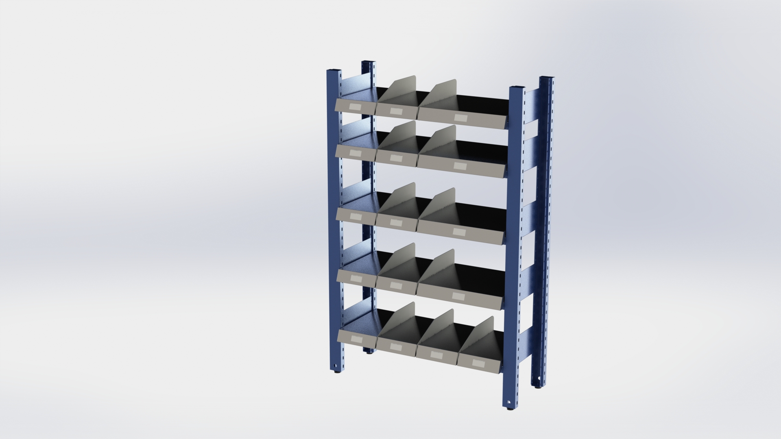
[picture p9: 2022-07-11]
hardware/regal/bilder/Regalsystem-001.JPG

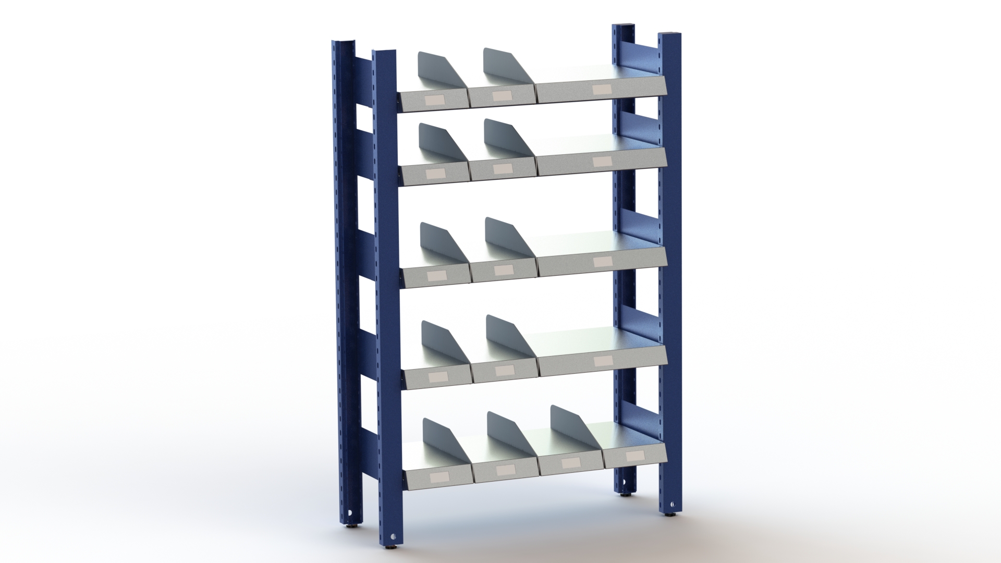
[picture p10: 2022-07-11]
hardware/regal/bilder/Regalsystem-002.JPG

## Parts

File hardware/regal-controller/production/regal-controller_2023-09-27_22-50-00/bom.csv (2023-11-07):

Designator | Footprint | Quantity | Value | LCSC Part #
C1 | 1206 | 1 | 0.1u
C2 | 1206 | 1 | 10u
C3 | 1206 | 1 | 10n
D1, D2, D3 | 1206 | 3 | LED
F1 | 1206 | 1 | Polyfuse 500mA
H1, H2, H3, H4 | MountingHole_3.2mm_M3 | 4 | MountingHole
J1 | USB_Micro-B_XKB_U254-051T-4BH83-F1S | 1 | USB_B_Micro
J2 | PinSocket_1x03_P2.54mm_Vertical | 1 | Conn_01x03
J3 | JST_SM04B-SRSS-TB(LF)(SN) | 1 | SM04B-SRSS-TB(LF)(SN)
R1, R2, R3 | 1206 | 3 | 1k
R4, R5 | 1206 | 2 | 2.2k
U1 | SOIC-16_3.9x9.9mm_P1.27mm | 1 | CH340C
U2 | SOIC-14_3.9x8.7mm_P1.27mm | 1 | ATtiny1614-SS

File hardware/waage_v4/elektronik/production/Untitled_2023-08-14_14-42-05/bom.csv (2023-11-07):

Designator | Footprint | Quantity | Value | LCSC Part #
C1 | 1206 | 1 | 10u
C2, C5, C6 | 1206 | 3 | 100n
C3 | 1206 | 1 | 330p
C4 | 1206 | 1 | 1µ
D1 | 1206 | 1 | LED
J1 | PinSocket_1x03_P2.54mm_Vertical | 1 | Conn_01x03
J2, J3 | JST_SM04B-SRSS-TB(LF)(SN) | 2 | SM04B-SRSS-TB(LF)(SN)
J4, J5, J6, J7 | SolderWire-0.1sqmm_1x03_P3.6mm_D0.4mm_OD1mm_Relief | 4 | Conn_01x03_Male
R1 | 1206 | 1 | 180
R2, R3 | 1206 | 2 | 47
U1 | SOIC-14_3.9x8.7mm_P1.27mm | 1 | ATtiny1614-SS
U2 | NAU7802SGI | 1 | NAU7802SGI

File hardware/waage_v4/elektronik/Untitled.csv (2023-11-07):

Source: | /Users/pbotte/Documents/git/zeitlos/hardware/waagen/waage_v4/elektronik/Untitled.kicad_sch
Date: | 2023 August 14, Monday 14:37:43
Tool: | Eeschema 7.0.5-0
Generator: | /Applications/KiCad/KiCad.app/Contents/SharedSupport/plugins/bom_csv_grouped_by_value_with_fp.py
Component Count: | 19
Ref | Qnty | Value | Cmp name | Footprint | Description | Vendor | DNP
C1 | 1 | 10u | C | Capacitor_SMD:C_1206_3216Metric | Unpolarized capacitor
C2, C5, C6 | 3 | 100n | C_Small | Capacitor_SMD:C_1206_3216Metric_Pad1.33x1.80mm_HandSolder | Unpolarized capacitor, small symbol
C3 | 1 | 330p | C_Small | Capacitor_SMD:C_1206_3216Metric_Pad1.33x1.80mm_HandSolder | Unpolarized capacitor, small symbol
C4 | 1 | 1µ | C_Small | Capacitor_SMD:C_1206_3216Metric_Pad1.33x1.80mm_HandSolder | Unpolarized capacitor, small symbol
D1 | 1 | LED | LED | LED_SMD:LED_1206_3216Metric_Pad1.42x1.75mm_HandSolder | Light emitting diode
J1 | 1 | Conn_01x03 | Conn_01x03 | Connector_PinSocket_2.54mm:PinSocket_1x03_P2.54mm_Vertical | Generic connector, single row, 01x03, script generated (kicad-library-utils/schlib/autogen/connector/)
J2, J3 | 2 | SM04B-SRSS-TB(LF)(SN) | SM04B-SRSS-TB(LF)(SN) | Quiicconnector:JST_SM04B-SRSS-TB(LF)(SN)
J4, J5, J6, J7 | 4 | Conn_01x03_Male | Conn_01x03_Pin | Connector_Wire:SolderWire-0.1sqmm_1x03_P3.6mm_D0.4mm_OD1mm_Relief | Generic connector, single row, 01x03, script generated
R1 | 1 | 180 | R | Resistor_SMD:R_1206_3216Metric_Pad1.30x1.75mm_HandSolder | Resistor
R2, R3 | 2 | 47 | R_Small | Resistor_SMD:R_1206_3216Metric_Pad1.30x1.75mm_HandSolder | Resistor, small symbol
U1 | 1 | ATtiny1614-SS | ATtiny1614-SS | Package_SO:SOIC-14_3.9x8.7mm_P1.27mm | 20MHz, 16kB Flash, 2kB SRAM, 256B EEPROM, SOIC-14
U2 | 1 | NAU7802SGI | NAU7802SGI | NAU:NAU7802SGI

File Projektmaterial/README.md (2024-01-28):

## TSE-Pflicht?

Nein! 

https://www.bundesfinanzministerium.de/Content/DE/FAQ/2020-02-18-steuergerechtigkeit-belegpflicht.html
```
Erfordert ein System, das grundsätzlich nur unbare Verkäufe zulässt (z.B. ein Webshop), den Einsatz einer TSE?
Wenn das System keine baren Zahlungsvorgänge vor Ort ermöglicht, muss das System nicht über eine TSE verfügen.
```
Und weiter, da es keine Kundenkarten gibt:
```Ist bei ausschließlicher Benutzung von aufladbaren Kundenkarten z. B. in Kantinen, auch dann eine Absicherung der Kassen mit einer TSE erforderlich, wenn die Aufwertung dieser aufladbaren Kundenkarten ausschließlich mit Debit- oder Kreditkarten oder anderer Form unbar erfolgen kann und auch eine bare Rückzahlung des Kundenguthabens ausgeschlossen ist?
Auch bei ausschließlich unbarer Aufwertung von aufladbaren Kundenkarten, stellen diese Einzweck- oder Mehrzweckgutscheine dar. Somit ergibt sich eine Kassenfunktion (ähnlich wie bei Bargeld), so dass eine Absicherung der Kassen mit einer TSE zwingend erfolgen muss. Für die Beurteilung der Kassenfunktion i. S. d. Nummer 1.2 des AEAO zu § 146a sind die unmittelbaren Zahlungsmöglichkeiten am Kassensystem maßgeblich.
```

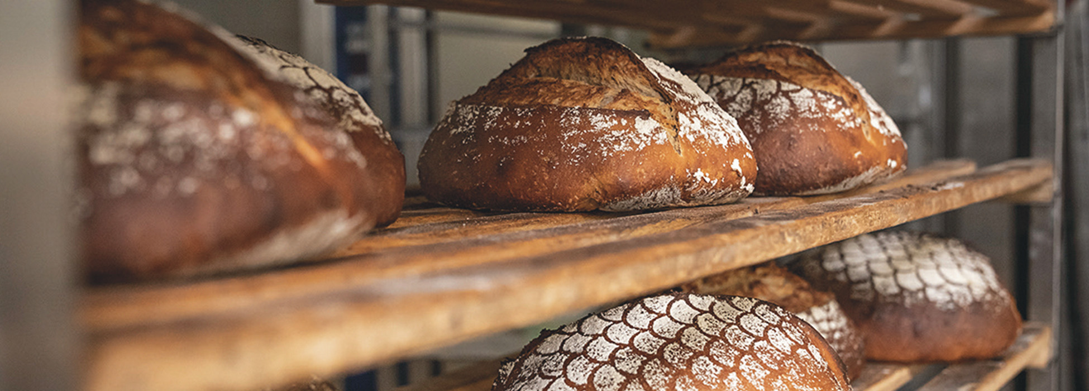
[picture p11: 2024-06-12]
software/waveshare-eink-pico/material/kern-korn-brotregal-auschnitt-2-1.jpg

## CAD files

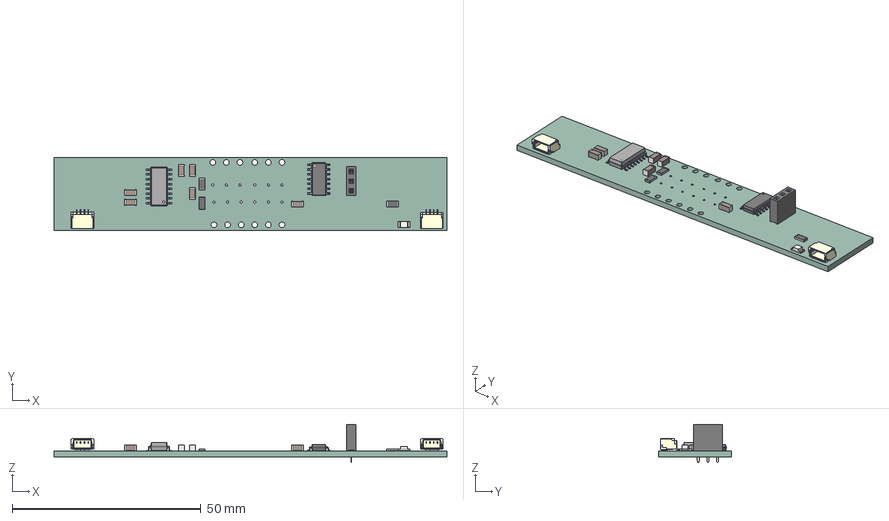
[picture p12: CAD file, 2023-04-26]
hardware/waage_v4/elektronik/Untitled.step
104.0 x 19.3 x 10.1 mm
PCB

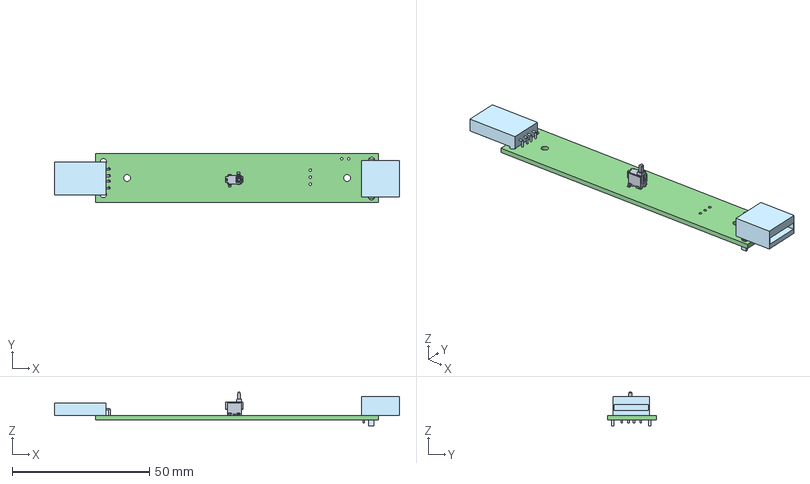
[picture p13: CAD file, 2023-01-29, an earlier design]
hardware/archive/waagen/waage_v3/elektronik/Untitled.step
125.9 x 17.8 x 12.4 mm
Untitled PCB

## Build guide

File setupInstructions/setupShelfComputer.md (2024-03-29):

# Regal-Computer

## Hardware
- [Raspberry Pi 3B](https://www.berrybase.de/raspberry-pi-co/raspberry-pi/boards/raspberry-pi-3-modell-b) (Leistungsfähig genug, und wird nicht so heiß, zieht nicht so viel Strom, läuft ohne Lüfter)
- micro SD-Card: [SanDisc Endurance 32GB](https://www.berrybase.de/raspberry-pi-co/raspberry-pi/speicherkarten/sandisk-high-endurance-microsdhc-uhs-i-u3-speicherkarte-43-adapter-32gb) (hält viele Schreibezyklen aus)
- Original-Gehäuse für Raspberry Pi
- [TP-Link PoE-Splitter 1GBit/s](https://www.idealo.de/preisvergleich/OffersOfProduct/2118892_-poe-splitter-tl-poe10r-tp-link.html)
- [Adapter-Kabel (Micro-B auf Hohlstecker Buchse)](https://www.berrybase.de/raspberry-pi-co/raspberry-pi/kabel-adapter/usb-kabel-adapter/adapterkabel-hohlstecker-buchse-5-5x2-1mm-micro-usb-b-stecker-schwarz-15cm) Adapterkabel Hohlstecker Buchse 5,5x2,1mm - Micro USB B Stecker schwarz 15cm
- HDMI-Kabel zum Monitor
- HDMI-Monitor mit VESA-Befestigungsmöglichkeit
- [D-Link USB-Hub, 7fach, mit PPS, mit Netzteil](https://www.idealo.de/preisvergleich/OffersOfProduct/97228.html)
- Langes Netzwerkkabel zum PoE-Switch
- 230V-Mehrfachsteckdosenleiste, genutzt für
  - Beleuchtung (Möglich sind: Zigbee-Lampen von Philips und IKEA)
  - Monitor
  - USB-HUB-Netzteil

### Alternative Konfiguration (Stand März 2024)
- Pi 4B oder 3B+
- POE+ Hat: [Spezifikation](https://datasheets.raspberrypi.com/poe/poe-plus-hat-product-brief.pdf)
  - Output power: 5 V DC/4 A
  - PoE Standard: PoE+ (IEEE 802.3at-2009 PoE)

Stand: März 2024
```bash
$ uname -a
Linux raspi-test 6.6.20+rpt-rpi-v8 #1 SMP PREEMPT Debian 1:6.6.20-1+rpt1 (2024-03-07) aarch64 GNU/Linux
```

Zügeln des Lüfters mittels:
```bash
$ dtoverlay -h rpi-poe-plus #Erläuterungen zu den Parametern
Name:   rpi-poe-plus

Info:   Raspberry Pi PoE+ HAT fan

Usage:  dtoverlay=rpi-poe-plus,<param>[=<val>]

Params: poe_fan_temp0           Temperature (in millicelcius) at which the fan
                                turns on (default 40000)
        poe_fan_temp0_hyst      Temperature delta (in millicelcius) at which
                                the fan turns off (default 2000)
...

$ sudo nano /boot/firmware/config.txt 
[all]
dtoverlay=rpi-poe-plus
dtparam=poe_fan_temp0=50000,poe_fan_temp0_hyst=5000
dtparam=poe_fan_temp1=55000,poe_fan_temp1_hyst=5000
dtparam=poe_fan_temp2=60000,poe_fan_temp2_hyst=5000
dtparam=poe_fan_temp3=65000,poe_fan_temp3_hyst=5000
```

Aktuelle Einstellung überprüfen mittels:
```bash
od -An --endian=big -td4 /proc/device-tree/thermal-zones/cpu-thermal/trips/trip?/temperature /proc/device-tree/thermal-zones/cpu-thermal/trips/trip?/hysteresis
       50000       55000       60000       65000
        5000        5000        5000        5000
```

Voll-Last-Test mit:
```bash
wget https://raw.githubusercontent.com/ssvb/cpuburn-arm/master/cpuburn-a53.S
gcc -o cpuburn-a53 cpuburn-a53.S
./cpuburn-a53 
```

CPU: Temperaturmessung in m°C
```bash
cat /sys/class/thermal/thermal_zone0/temp
```

HAT gelieferter Strom in muA
```bash
$ cat /sys/devices/platform/rpi-poe-power-supply/power_supply/rpi-poe/current_now
577000
```

## Software-Konfiguration

- Netzwerkname: `shop-shelf-01`
- Anzeige einer Webseite, Übermittlung des Hostnamens -> Weiterleitung zur angepassten Webseite
- Anzeige [im Kiosk-Modus](https://itrig.de/index.php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):
  - Maus weg
  - Vollbild
  - kein Bildschirmschoner
  ```bash
  sudo apt-get install unclutter
  sudo nano /etc/xdg/lxsession/LXDE-pi/autostart
  #Mauszeiger weg:
  @unclutter
  #Bildschirmschoner deaktivieren 
  #(die folgende Zeile also suchen und auskommentieren)
  #@xscreensaver -no-splash 

  #Bildschirm nicht ausschalten
  @xset s off
  @xset -dpms
  @xset s noblank
  #Browser starten
  @chromium-browser --kiosk http://shop-master/?hostname= 
  ```
- Abends und morgens den HDMI-Bildschirm [ein-/ausschalten](https://www.elektronik-kompendium.de/sites/raspberry-pi/2111101.htm) (nicht nicht getestet).
- Am Ende: Aktivierung des Overlay-FS

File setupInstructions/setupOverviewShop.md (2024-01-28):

# Übersicht über den gesamten Aufbau

Es gibt
- Einen Kontroll-Rechner, `shop-master`
- Einen Rechner für den Einlass und Werbung, `shop-doordisplay`
- Für jedes Regal einen Rechner, `shop-shelf-01`
  Die Waagen innerhalb eines Regals sind an den jeweiligen Regal-Rechner angeschlossen.
- Überwachungskameras
- Einen Router (Fritzbox, UNifi Router, etc.) für die Verbindung nach Außen.
- PoE-Switch für die Versorgung von Rechnern, Kameras, etc.

## Netzwerk

- Kontroll-Netz, 192.168.10.x/24

## Kontroll-Rechner:
- gut gesichert, nicht im Kundenbereich
- Hat eine ordentliche Festplatte oder SSD
- Bestimmt: Belegung de Ladens (Belegt/Frei)
- Berechnung des Warenkorbs

### Services:
- TimeScale-DB für 
  - Überwachungsdaten (Temperatur-Protokolle) und
  - Daten der Waagen (somit kann später eine Reklamation besser nachvollzogen werden)
- MQTT-Service
- HTTP-Server für Webseiten, die die `shop-shelf`-Computer darstellen
- Datenbank für Produkte und Einkäufe
- Am besten ein normaler Computer mit Standard-Hardware, abgesichert per USV.
- Bietet einen Wartungszugang

## Rechner mit Display am Eingang
- Netzwerkname: `shop-doordisplay`
- Zeigt den aktuellen Status an
- Immer Werbung für den Laden anzeigen.

## Pro Regal
- Zuleitung von 230V-Strom und Netzwerkkabel
- [Rechner mit USB-Hub und Waagen](setupShelfComputer.md)

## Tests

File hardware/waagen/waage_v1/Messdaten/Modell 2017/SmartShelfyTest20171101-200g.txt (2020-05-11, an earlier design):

SmartShelfy	1321477	8491321	8667116	8932268	8568673	
SmartShelfy	1321979	8491389	8667143	8932287	8568674	
SmartShelfy	1322480	8491770	8666690	8931811	8569228	
SmartShelfy	1322981	8491784	8666623	8931681	8569244	
SmartShelfy	1323482	8491375	8667071	8932097	8568769	
SmartShelfy	1323983	8491505	8666924	8932016	8568897	
SmartShelfy	1324485	8490580	8667957	8933020	8567872	
SmartShelfy	1324986	8490174	8668322	8933347	8567586	
SmartShelfy	1325487	8492103	8666812	8931653	8569487	
SmartShelfy	1325988	8491890	8666593	8931583	8569303	
SmartShelfy	1326489	8491423	8667081	8932213	8568769	
SmartShelfy	1326991	8492213	8665209	8975003	8571164	
SmartShelfy	1327492	8491864	8665868	8975236	8570817	
SmartShelfy	1327993	8492346	8665505	8974681	8570981	
SmartShelfy	1328494	8492897	8664777	8974114	8571855	
SmartShelfy	1328995	8492599	8665027	8974427	8571598	
SmartShelfy	1329496	8493520	8664180	8973535	8572543	
SmartShelfy	1329997	8493301	8664316	8973766	8572287	
SmartShelfy	1330498	8494089	8663544	8972972	8573064	
SmartShelfy	1331000	8494034	8663712	8973056	8573030	
SmartShelfy	1331501	8492552	8665956	8930946	8570115	
SmartShelfy	1332002	8492616	8665943	8930979	8570051	
SmartShelfy	1332503	8492767	8665075	8970088	8576139	
SmartShelfy	1333005	8492738	8665212	8970107	8576105	
SmartShelfy	1333506	8492831	8665120	8970026	8576176	
SmartShelfy	1334007	8492208	8665584	8970673	8575564	
SmartShelfy	1334508	8493057	8664820	8969704	8576176	
SmartShelfy	1335009	8492812	8665199	8970051	8576165	
SmartShelfy	1335510	8493059	8664925	8969857	8576371	
SmartShelfy	1336011	8493107	8664825	8969830	8576344	
SmartShelfy	1336513	8493079	8664819	8969788	8576321	
SmartShelfy	1337014	8493103	8664837	8969796	8576377	
SmartShelfy	1338016	8492148	8666494	8931350	8569682	
SmartShelfy	1338517	8492115	8666532	8935132	8569705	
SmartShelfy	1339018	8492630	8665074	8966046	8580128	
SmartShelfy	1339519	8492934	8664801	8965819	8580478	
SmartShelfy	1340020	8492028	8665607	8966753	8579646	
SmartShelfy	1340521	8491005	8666719	8967695	8578589	
SmartShelfy	1341022	8491026	8666621	8967604	8578585	
SmartShelfy	1341524	8491364	8666445	8967414	8578884	
SmartShelfy	1342025	8491871	8665802	8966865	8579496	
SmartShelfy	1342526	8490965	8666569	8967503	8578839	
SmartShelfy	1343027	8492338	8665860	8966671	8579362	
SmartShelfy	1343528	8493146	8664569	8965575	8580741	
SmartShelfy	1344030	8493539	8664579	8959548	8580764	
SmartShelfy	1344531	8492985	8665546	8930466	8570546	
SmartShelfy	1345032	8493328	8665231	8930154	8570803	
SmartShelfy	1345533	8493458	8665076	8929989	8571089	
SmartShelfy	1346034	8493566	8665045	8929938	8571125	
SmartShelfy	1346536	8493513	8665017	8929961	8571058	
SmartShelfy	1347037	8493777	8663986	8960776	8585448	
SmartShelfy	1347538	8493924	8663875	8960617	8585565	
SmartShelfy	1348039	8493923	8663929	8960657	8585595	
SmartShelfy	1348540	8493705	8664089	8960901	8585365	
SmartShelfy	1349042	8493414	8664463	8961178	8585122	
SmartShelfy	1349543	8493079	8664740	8961486	8584757	
SmartShelfy	1350044	8493027	8664817	8961530	8584681	
SmartShelfy	1350545	8493155	8664663	8961411	8584747	
SmartShelfy	1351046	8493436	8664427	8961148	8584960	
SmartShelfy	1351548	8493531	8664948	8930004	8571024	
SmartShelfy	1352050	8493399	8665070	8930107	8570893	
SmartShelfy	1352551	8493416	8665014	8933593	8572277	
SmartShelfy	1353053	8493005	8664720	8957306	8589039	
SmartShelfy	1353554	8492932	8664823	8957356	8588962	
SmartShelfy	1354055	8493027	8664788	8957370	8589024	
SmartShelfy	1354556	8493255	8664522	8957131	8589327	
SmartShelfy	1355057	8493496	8664273	8956883	8589529	
SmartShelfy	1355559	8493682	8664001	8956716	8589680	
SmartShelfy	1356060	8493623	8664123	8956718	8589675	
SmartShelfy	1356561	8493429	8664316	8956931	8589350	
SmartShelfy	1357062	8493274	8664456	8957058	8589360	
SmartShelfy	1357564	8494387	8663448	8956031	8590380	
SmartShelfy	1358064	8494776	8663059	8955681	8590794	
SmartShelfy	1358566	8494790	8662889	8955583	8590922	
SmartShelfy	1359067	8494631	8663082	8955685	8590640	
SmartShelfy	1359568	8493769	8663983	8956643	8589779	
SmartShelfy	1360069	8493742	8664642	8929667	8571326	
SmartShelfy	1360570	8493636	8664836	8929845	8571347	
SmartShelfy	1361071	8492905	8665018	8953376	8593016	
SmartShelfy	1361573	8492804	8665136	8953454	8592952	
SmartShelfy	1362074	8493163	8664720	8953016	8593326	
SmartShelfy	1362575	8493197	8664759	8953047	8593351	
SmartShelfy	1363076	8493368	8664530	8952865	8593456	
SmartShelfy	1363577	8493454	8664445	8952746	8593622	
SmartShelfy	1364079	8493434	8664420	8952783	8593586	
SmartShelfy	1364580	8493463	8664454	8952797	8593544	
SmartShelfy	1365081	8493368	8664492	8952818	8593546	
SmartShelfy	1365582	8493315	8664608	8952941	8593465	
SmartShelfy	1366083	8493341	8664502	8952813	8593558	
SmartShelfy	1366585	8493523	8664418	8941454	8592015	
SmartShelfy	1367086	8494726	8663869	8928882	8572188	
SmartShelfy	1367587	8494107	8664534	8957655	8608761	
SmartShelfy	1368088	8493591	8664248	8949691	8601163	
SmartShelfy	1368589	8493609	8664068	8948474	8598088	
SmartShelfy	1369091	8493150	8664606	8948898	8597593	
SmartShelfy	1369592	8494336	8663327	8947692	8598728	
SmartShelfy	1370093	8494019	8663692	8947987	8598466	
SmartShelfy	1370594	8493960	8663746	8948068	8598468	
SmartShelfy	1371096	8493890	8663865	8948129	8598334	
SmartShelfy	1371597	8493849	8663893	8948240	8598267	
SmartShelfy	1372098	8493805	8663950	8948228	8598300	
SmartShelfy	1372599	8493692	8664063	8948428	8598137	
SmartShelfy	1373100	8494766	8663707	8928780	8572312	
SmartShelfy	1373602	8494873	8663570	8928684	8572336	
SmartShelfy	1374103	8495013	8663455	8928581	8572532	
SmartShelfy	1374604	8495133	8663366	8928527	8572584	
SmartShelfy	1375105	8495092	8663365	8928593	8572484	
SmartShelfy	1375606	8495043	8663391	8928542	8572571	
SmartShelfy	1376108	8493832	8664925	8947573	8607557	
SmartShelfy	1376609	8493229	8664989	8945089	8602580	
SmartShelfy	1377111	8493243	8664856	8944628	8601730	
SmartShelfy	1377612	8492939	8665112	8944857	8601498	
SmartShelfy	1378113	8493284	8664809	8944541	8601827	
SmartShelfy	1378614	8493405	8664642	8944352	8601962	
SmartShelfy	1379115	8493624	8664493	8944205	8602184	
SmartShelfy	1379616	8493498	8664585	8944328	8602097	
SmartShelfy	1380118	8493789	8664301	8944060	8602397	
SmartShelfy	1380619	8493646	8664480	8944227	8602135	
SmartShelfy	1381120	8493452	8664634	8944414	8601992	
SmartShelfy	1381621	8493339	8664748	8944505	8601863	
SmartShelfy	1382122	8493301	8664855	8944579	8601754	
SmartShelfy	1382624	8493432	8664969	8945100	8602954	
SmartShelfy	1383125	8494494	8664099	8929524	8572281	
SmartShelfy	1383626	8494690	8663934	8928864	8572172	
SmartShelfy	1384127	8493882	8664409	8938941	8603981	
SmartShelfy	1384628	8492958	8664862	8940561	8605969	
SmartShelfy	1385130	8493010	8664843	8940584	8605954	
SmartShelfy	1385631	8493909	8664153	8939666	8606894	
SmartShelfy	1386132	8494429	8663392	8939325	8607449	
SmartShelfy	1386633	8493353	8664489	8939904	8606244	
SmartShelfy	1387134	8491945	8665712	8941546	8604952	
SmartShelfy	1387636	8492005	8665815	8941461	8604999	
SmartShelfy	1388137	8492166	8665708	8941436	8605199	
SmartShelfy	1388638	8492322	8665580	8941264	8605286	
SmartShelfy	1389139	8492225	8665573	8941318	8605321	
SmartShelfy	1389640	8493067	8665238	8932600	8585440	
SmartShelfy	1390142	8494074	8664532	8929545	8571521	
SmartShelfy	1390643	8492942	8665298	8937161	8618259	
SmartShelfy	1391144	8491991	8665788	8938067	8611977	
SmartShelfy	1391645	8491489	8666250	8937869	8608874	
SmartShelfy	1392146	8491710	8666054	8937719	8608921	
SmartShelfy	1392648	8492311	8665363	8937001	8609640	
SmartShelfy	1393149	8491493	8666357	8938001	8608793	
SmartShelfy	1393650	8490998	8666769	8938316	8608285	
SmartShelfy	1394151	8491079	8666613	8938260	8608274	
SmartShelfy	1394652	8491327	8666366	8938040	8608339	
SmartShelfy	1395154	8491667	8665925	8937593	8608915	
SmartShelfy	1395655	8491795	8665903	8937502	8609171	
SmartShelfy	1396156	8492077	8665711	8937407	8609627	
SmartShelfy	1396657	8492169	8665617	8937490	8610340	
SmartShelfy	1397158	8494237	8664339	8929316	8571722	
SmartShelfy	1397659	8494183	8664651	8929848	8578603	
SmartShelfy	1398161	8489756	8669967	8936727	8659631	
SmartShelfy	1398662	8491758	8665932	8933641	8614104	
SmartShelfy	1399163	8490010	8667603	8935023	8611755	
SmartShelfy	1399664	8490970	8666801	8934057	8612427	
SmartShelfy	1400165	8493921	8663934	8931349	8615402	
SmartShelfy	1400666	8492902	8664903	8932274	8614468	
SmartShelfy	1401168	8492169	8665468	8933062	8613811	
SmartShelfy	1401669	8491928	8665807	8933266	8613402	
SmartShelfy	1402170	8492242	8665513	8932935	8613715	
SmartShelfy	1402671	8492275	8665517	8932885	8613783	
SmartShelfy	1403172	8492278	8665542	8932930	8613796	
SmartShelfy	1403673	8493492	8664698	8929606	8592494	
SmartShelfy	1404174	8494245	8664264	8929464	8571584	
SmartShelfy	1404676	8493844	8664769	8929773	8571306	
SmartShelfy	1405177	8493309	8665101	8930082	8570995	
SmartShelfy	1405678	8492622	8665969	8931033	8569992	
SmartShelfy	1406179	8492897	8666196	8932442	8569935	
SmartShelfy	1406681	8504815	8664306	8967524	8568525	
SmartShelfy	1407182	8503998	8664424	8967165	8568176	
SmartShelfy	1407683	8503393	8665363	8967821	8567435	
SmartShelfy	1408184	8504099	8664565	8966900	8568362	
SmartShelfy	1408685	8504672	8664016	8966495	8568876	
SmartShelfy	1409186	8504724	8663997	8966554	8568815	
SmartShelfy	1409687	8505135	8663625	8966069	8569279	
SmartShelfy	1410188	8504564	8664086	8966632	8568761	
SmartShelfy	1410690	8505352	8663292	8965660	8569181	
SmartShelfy	1411191	8505053	8663553	8966292	8569177	
SmartShelfy	1411692	8504524	8664130	8966579	8568697	
SmartShelfy	1412193	8504765	8663969	8966400	8568920	
SmartShelfy	1412694	8504433	8664272	8966825	8568580	
SmartShelfy	1413195	8504698	8664025	8966504	8568841	
SmartShelfy	1413697	8504684	8664009	8966523	8568881	
SmartShelfy	1414198	8504765	8663979	8966416	8568957	
SmartShelfy	1414699	8504668	8664127	8966512	8568873	
SmartShelfy	1415200	8492637	8665907	8930808	8570091	
SmartShelfy	1415701	8513131	8663394	9015363	8572972	
SmartShelfy	1416202	8503000	8665610	8964354	8571211	
SmartShelfy	1416703	8503244	8665262	8963774	8571591	
SmartShelfy	1417204	8503432	8665208	8963724	8571631	
SmartShelfy	1417705	8503118	8665477	8963954	8571365	
SmartShelfy	1418207	8503067	8665570	8964102	8571309	
SmartShelfy	1418708	8503116	8665420	8963955	8571325	
SmartShelfy	1419209	8503143	8665513	8963955	8571368	
SmartShelfy	1419710	8503182	8665487	8963934	8571371	
SmartShelfy	1420212	8503041	8665606	8964139	8571209	
SmartShelfy	1420713	8502505	8666135	8964597	8570699	
SmartShelfy	1421214	8502346	8666277	8964912	8570565	
SmartShelfy	1421715	8491692	8666930	8931839	8569063	
SmartShelfy	1422216	8491714	8666813	8931857	8569160	
SmartShelfy	1422718	8510465	8668428	8966346	8574011	
SmartShelfy	1423219	8530437	8670687	9041012	8583591	
SmartShelfy	1423720	8501199	8667631	8961815	8573351	
SmartShelfy	1424221	8501434	8667373	8961571	8573741	
SmartShelfy	1424722	8501688	8667167	8961300	8573978	
SmartShelfy	1425223	8501611	8667156	8961289	8573885	
SmartShelfy	1425724	8501589	8667190	8961332	8573960	
SmartShelfy	1426226	8501868	8666859	8961077	8574234	
SmartShelfy	1426727	8501159	8667560	8961791	8573509	
SmartShelfy	1427228	8501202	8667619	8961763	8573512	
SmartShelfy	1427729	8501125	8667669	8961877	8573358	
SmartShelfy	1428230	8500955	8667807	8961899	8573269	
SmartShelfy	1428732	8501196	8667786	8963010	8573349	
SmartShelfy	1429233	8491575	8666988	8931985	8568974	
SmartShelfy	1429734	8494404	8668078	8940651	8575520	
SmartShelfy	1430235	8499992	8668634	8958744	8576600	
SmartShelfy	1430736	8499970	8668567	8958799	8576657	
SmartShelfy	1431237	8500376	8668115	8958326	8577148	
SmartShelfy	1431738	8500695	8667972	8958125	8577337	
SmartShelfy	1432240	8500894	8667671	8957819	8577584	
SmartShelfy	1432741	8500925	8667577	8957774	8577594	
SmartShelfy	1433242	8501067	8667559	8957800	8577661	
SmartShelfy	1433743	8501134	8667469	8957655	8577819	
SmartShelfy	1434244	8501173	8667310	8957531	8577884	
SmartShelfy	1434745	8501104	8667480	8957740	8577852	
SmartShelfy	1435247	8493101	8665378	8930419	8570517	
SmartShelfy	1435748	8502822	8667076	8957019	8575666	
SmartShelfy	1436249	8500405	8668185	8954297	8581236	
SmartShelfy	1436750	8500603	8667943	8953861	8581484	
SmartShelfy	1437251	8500454	8668070	8954168	8581313	
SmartShelfy	1437753	8500371	8668269	8954221	8581220	
SmartShelfy	1438254	8500252	8668389	8954393	8581084	
SmartShelfy	1438755	8500411	8668147	8954061	8581266	
SmartShelfy	1439256	8500709	8667822	8953778	8581626	
SmartShelfy	1439757	8500806	8667806	8953814	8581605	
SmartShelfy	1440259	8500800	8667818	8953834	8581654	
SmartShelfy	1440760	8500860	8667757	8953768	8581723	
SmartShelfy	1441261	8500660	8667871	8953865	8581585	
SmartShelfy	1441762	8495314	8666816	8936425	8572809	
SmartShelfy	1442264	8496313	8666240	8934145	8573596	
SmartShelfy	1442766	8509919	8674399	8969169	8599576	
SmartShelfy	1443267	8499464	8668958	8950810	8584500	
SmartShelfy	1443768	8499492	8668979	8950848	8584607	
SmartShelfy	1444269	8499676	8668841	8950701	8584678	
SmartShelfy	1444770	8499899	8668644	8950491	8584982	
SmartShelfy	1445271	8499963	8668581	8950403	8585016	
SmartShelfy	1445773	8499631	8668827	8950763	8584641	
SmartShelfy	1446274	8499552	8668887	8950802	8584672	
SmartShelfy	1446775	8499598	8668817	8950723	8584746	
SmartShelfy	1447276	8499617	8668912	8950835	8584583	
SmartShelfy	1447777	8500823	8669654	8953514	8586966	
SmartShelfy	1448278	8493883	8664366	8929623	8571335	
SmartShelfy	1448780	8493976	8664348	8929633	8571496	
SmartShelfy	1449281	8499974	8673251	8960934	8606648	
SmartShelfy	1449782	8498356	8670043	8947763	8587631	
SmartShelfy	1450283	8498546	8669891	8947553	8587830	
SmartShelfy	1450784	8498602	8669826	8947433	8588029	
SmartShelfy	1451286	8498541	8669870	8947505	8587953	
SmartShelfy	1451787	8498669	8669737	8947390	8587978	
SmartShelfy	1452288	8498559	8669921	8947549	8587881	
SmartShelfy	1452789	8498575	8669934	8947511	8587827	
SmartShelfy	1453290	8498597	8669786	8947462	8587970	
SmartShelfy	1453792	8498754	8669727	8947390	8588004	
SmartShelfy	1454293	8498835	8669640	8947301	8588124	
SmartShelfy	1454794	8498806	8669681	8947318	8588092	
SmartShelfy	1455295	8498834	8669582	8947293	8588104	
SmartShelfy	1455796	8498856	8669608	8947277	8588144	
SmartShelfy	1456298	8498857	8669606	8947246	8588140	
SmartShelfy	1456799	8498847	8669600	8947273	8588169	
SmartShelfy	1457300	8500330	8668174	8945904	8589672	
SmartShelfy	1457801	8497849	8666353	8939494	8585056	
SmartShelfy	1458302	8495949	8664730	8933137	8577650	
SmartShelfy	1458804	8502710	8678483	8966112	8624832	
SmartShelfy	1459305	8498435	8670054	8943597	8592031	
SmartShelfy	1459806	8498547	8669920	8943455	8592191	
SmartShelfy	1460307	8498772	8669775	8943259	8592310	
SmartShelfy	1460808	8498710	8669735	8943203	8592365	
SmartShelfy	1461309	8498738	8669770	8943316	8592278	
SmartShelfy	1461810	8498752	8669568	8943176	8592447	
SmartShelfy	1462311	8498966	8669474	8942918	8592656	
SmartShelfy	1462813	8499019	8669393	8942958	8592618	
SmartShelfy	1463314	8499052	8669353	8942920	8592648	
SmartShelfy	1463815	8499000	8669481	8942955	8592619	
SmartShelfy	1464316	8498974	8669435	8942941	8592664	
SmartShelfy	1464817	8498996	8669409	8942883	8592579	
SmartShelfy	1465319	8499020	8669479	8943025	8592603	
SmartShelfy	1465820	8499014	8669734	8946826	8594803	
SmartShelfy	1466321	8495308	8662902	8928110	8572801	
SmartShelfy	1466822	8495499	8662659	8927948	8573046	
SmartShelfy	1467323	8495576	8662589	8927779	8573144	
SmartShelfy	1467824	8495575	8662536	8927738	8573128	
SmartShelfy	1468325	8498714	8674024	8947502	8609345	
SmartShelfy	1468826	8497595	8672799	8940295	8599155	
SmartShelfy	1469327	8497680	8671583	8940951	8595490	
SmartShelfy	1469829	8496510	8671981	8941196	8594415	
SmartShelfy	1470330	8497184	8671208	8940509	8595197	
SmartShelfy	1470831	8496742	8671695	8940910	8594733	
SmartShelfy	1471332	8496547	8671973	8941195	8594392	
SmartShelfy	1471833	8496383	8672109	8941362	8594274	
SmartShelfy	1472333	8496361	8672103	8941362	8594171	
SmartShelfy	1472834	8496328	8672120	8941407	8594190	
SmartShelfy	1473335	8496332	8672151	8941327	8594175	
SmartShelfy	1473836	8496886	8673523	8942859	8596571	
SmartShelfy	1474338	8496101	8680127	8945037	8616442	
SmartShelfy	1474839	8496606	8681436	8948745	8626548	
SmartShelfy	1475340	8494834	8673718	8938626	8596893	
SmartShelfy	1475841	8495130	8673411	8938334	8597240	
SmartShelfy	1476342	8495015	8673573	8938322	8597174	
SmartShelfy	1476844	8494754	8673916	8938402	8596864	
SmartShelfy	1477345	8493844	8674782	8939545	8595827	
SmartShelfy	1477847	8493399	8675225	8939990	8595489	
SmartShelfy	1478348	8493285	8675339	8940126	8595351	
SmartShelfy	1478849	8493317	8675292	8940085	8595362	
SmartShelfy	1479350	8493416	8675187	8939971	8595434	
SmartShelfy	1479851	8493435	8675261	8939996	8595462	
SmartShelfy	1480352	8493341	8675278	8940072	8595371	
SmartShelfy	1480854	8493178	8669701	8938023	8585876	
SmartShelfy	1481355	8491898	8666300	8931339	8569463	
SmartShelfy	1481856	8492869	8673882	8937623	8602078	
SmartShelfy	1482357	8492046	8676856	8937110	8598094	
SmartShelfy	1482858	8492301	8676601	8936869	8598341	
SmartShelfy	1483360	8493279	8675803	8935837	8599346	
SmartShelfy	1483861	8493931	8674968	8935284	8600035	
SmartShelfy	1484362	8493226	8675731	8936081	8599258	
SmartShelfy	1484863	8493242	8675666	8935992	8599250	
SmartShelfy	1485364	8492921	8675992	8936343	8598972	
SmartShelfy	1485865	8493132	8675798	8936138	8599171	
SmartShelfy	1486367	8493153	8675800	8936152	8599132	
SmartShelfy	1486868	8492997	8675910	8936286	8599062	
SmartShelfy	1487369	8492862	8675985	8936336	8598920	
SmartShelfy	1487870	8492659	8676257	8936601	8598627	
SmartShelfy	1488371	8492459	8676493	8936675	8598518	
SmartShelfy	1488872	8492395	8676481	8936766	8598463	
SmartShelfy	1489373	8492417	8676460	8936813	8598419	
SmartShelfy	1489875	8492611	8676334	8936705	8598647	
SmartShelfy	1490376	8492401	8676550	8936818	8598489	
SmartShelfy	1490877	8492562	8676493	8936842	8598664	
SmartShelfy	1491378	8492072	8666163	8931305	8569552	
SmartShelfy	1491879	8492070	8666216	8931355	8569464	
SmartShelfy	1492380	8491930	8666418	8931530	8569411	
SmartShelfy	1492881	8491786	8666432	8931515	8569278	
SmartShelfy	1493383	8491015	8679418	8934596	8605058	
SmartShelfy	1493884	8490898	8678437	8934103	8603345	
SmartShelfy	1494385	8491538	8677583	8933641	8601522	
SmartShelfy	1494886	8491683	8677431	8933489	8601726	
SmartShelfy	1495387	8491752	8677291	8933357	8601806	
SmartShelfy	1495888	8491808	8677304	8933364	8601806	
SmartShelfy	1496389	8491743	8677344	8933408	8601808	
SmartShelfy	1496891	8491859	8677253	8933325	8601898	
SmartShelfy	1497392	8491812	8677246	8933287	8601903	
SmartShelfy	1497893	8491890	8677258	8933233	8601904	
SmartShelfy	1498394	8491824	8677213	8933273	8601890	
SmartShelfy	1498895	8491827	8677207	8933253	8601970	
SmartShelfy	1499397	8491557	8677417	8933559	8601608	
SmartShelfy	1499898	8491245	8681654	8934457	8609278	
SmartShelfy	1500399	8491749	8666930	8931753	8572716	
SmartShelfy	1500900	8491132	8669260	8931519	8579099	
SmartShelfy	1501401	8489248	8682766	8931004	8626488	
SmartShelfy	1501903	8489681	8679073	8931112	8604438	
SmartShelfy	1502404	8490051	8678811	8930813	8604747	
SmartShelfy	1502905	8490165	8678532	8930609	8604858	
SmartShelfy	1503406	8490260	8678467	8930531	8604906	
SmartShelfy	1503907	8490326	8678287	8930491	8605022	
SmartShelfy	1504408	8490449	8678288	8930344	8605120	
SmartShelfy	1504909	8490480	8678201	8930321	8605157	
SmartShelfy	1505411	8490495	8678298	8930347	8605188	
SmartShelfy	1505912	8490454	8678257	8930380	8605105	
SmartShelfy	1506413	8490372	8678382	8930402	8605050	
SmartShelfy	1506914	8490683	8677958	8930064	8605323	
SmartShelfy	1507415	8490074	8678616	8930727	8604714	
SmartShelfy	1507917	8489087	8679896	8931131	8606881	
SmartShelfy	1508418	8491125	8667171	8932382	8568449	
SmartShelfy	1508919	8491758	8666564	8931511	8568981	
SmartShelfy	1509420	8490177	8668454	8933531	8567321	
SmartShelfy	1509921	8545817	8665321	8989256	8564104	
SmartShelfy	1510422	8543040	8666075	8974483	8564128	
SmartShelfy	1510924	8513605	8666543	8956958	8566212	
SmartShelfy	1511425	8513843	8666220	8957172	8566454	
SmartShelfy	1511926	8513596	8666347	8957356	8566342	
SmartShelfy	1512427	8513197	8666991	8957932	8565785	
SmartShelfy	1512928	8512762	8667298	8958279	8565386	
SmartShelfy	1513429	8513015	8667044	8958034	8565617	
SmartShelfy	1513930	8512886	8667141	8958202	8565529	
SmartShelfy	1514431	8512959	8667108	8958008	8565562	
SmartShelfy	1514932	8512852	8667232	8958215	8565496	
SmartShelfy	1515434	8512705	8667425	8958391	8565314	
SmartShelfy	1515935	8513353	8666718	8957718	8565973	
SmartShelfy	1516436	8512483	8667585	8958543	8565167	
SmartShelfy	1516937	8512458	8667670	8958591	8565066	
SmartShelfy	1517438	8489421	8668996	8933975	8566729	
SmartShelfy	1517939	8489602	8668790	8933790	8566978	
SmartShelfy	1518440	8489697	8668657	8933729	8567016	
SmartShelfy	1518941	8522288	8670174	8968236	8567001	
SmartShelfy	1519442	8518627	8670460	8963890	8566464	
SmartShelfy	1519944	8510533	8669968	8956743	8566793	
SmartShelfy	1520445	8512374	8668006	8954874	8568572	
SmartShelfy	1521447	8513868	8666600	8953388	8570151	
SmartShelfy	1521948	8513877	8666534	8953412	8570156	
SmartShelfy	1522950	8513827	8666582	8953438	8570132	
SmartShelfy	1523451	8513855	8666547	8953395	8570151	
SmartShelfy	1523952	8513884	8666477	8953334	8570233	
SmartShelfy	1524453	8513912	8666447	8953297	8570259	
SmartShelfy	1524955	8514031	8666423	8953250	8570268	
SmartShelfy	1525957	8514066	8666370	8953202	8570330	
SmartShelfy	1526458	8513903	8666425	8953362	8570264	
SmartShelfy	1526959	8513816	8666522	8953414	8570232	
SmartShelfy	1527460	8513965	8666414	8953309	8570280	
SmartShelfy	1527961	8513952	8666370	8953338	8570334	
SmartShelfy	1528463	8513968	8666427	8953273	8570277	
SmartShelfy	1528964	8514086	8666392	8953261	8570357	
SmartShelfy	1529465	8513565	8666908	8953799	8569780	
SmartShelfy	1529966	8512987	8667487	8954424	8569169	
SmartShelfy	1530467	8512886	8667570	8954513	8388480	
SmartShelfy	1530969	8512857	8667536	8954428	8569157	
SmartShelfy	1531470	8513123	8667332	8954146	8569420	
SmartShelfy	1531971	8513359	8667115	8953994	8569611	
SmartShelfy	1532472	8513359	8667054	8953953	8569660	
SmartShelfy	1532973	8513520	8666915	8953748	8569803	
SmartShelfy	1533474	8513347	8667051	8953962	8569660	
SmartShelfy	1533975	8513388	8667040	8953954	8569650	
SmartShelfy	1534476	8513661	8667406	8954823	8569209	
SmartShelfy	1534978	8491363	8667084	8932176	8568731	
SmartShelfy	1535479	8491620	8666927	8931953	8568982	
SmartShelfy	1535980	8493302	8667036	8934655	8570199	
SmartShelfy	1536481	8510007	8670403	8952964	8570711	
SmartShelfy	1536982	8510507	8669923	8952555	8571103	
SmartShelfy	1537484	8511728	8668852	8951308	8572432	
SmartShelfy	1537985	8511501	8668844	8951535	8572307	
SmartShelfy	1538486	8511583	8668814	8951523	8572242	
SmartShelfy	1538987	8511578	8668777	8951460	8572330	
SmartShelfy	1539488	8511528	8668780	8951526	8572237	
SmartShelfy	1539989	8511644	8668730	8951398	8572349	
SmartShelfy	1540490	8511486	8668901	8951552	8572168	
SmartShelfy	1540991	8511610	8668727	8951395	8572303	
SmartShelfy	1541492	8511570	8668867	8951607	8572157	
SmartShelfy	1541994	8511513	8668815	8951516	8572167	
SmartShelfy	1542495	8511690	8668703	8951401	8572390	
SmartShelfy	1542996	8511465	8668862	8951572	8572153	
SmartShelfy	1543497	8511401	8669008	8951668	8572118	
SmartShelfy	1543998	8505857	8668854	8951206	8571117	
SmartShelfy	1544500	8492114	8666499	8931419	8569505	
SmartShelfy	1545000	8514597	8674847	8958124	8574606	
SmartShelfy	1545502	8508890	8671800	8949739	8573574	
SmartShelfy	1546003	8509291	8671493	8949429	8573927	
SmartShelfy	1546504	8510177	8670581	8948662	8574679	
SmartShelfy	1547005	8510728	8669915	8947896	8575532	
SmartShelfy	1547506	8510425	8670142	8948181	8575288	
SmartShelfy	1548007	8511122	8669594	8947547	8575922	
SmartShelfy	1548508	8510489	8670100	8948126	8575388	
SmartShelfy	1549010	8509577	8671161	8949097	8574366	
SmartShelfy	1549511	8509934	8670815	8948750	8574634
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

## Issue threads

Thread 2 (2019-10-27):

Update-Überprüfung für Arduino einfügen

pbotte, 2019-10-27:
Beim Start (und in Regelmäßigen Abständen? aber wohl besser nicht) überprüft der Scale Controller, ob es eine neue Firmware für den Arduino gibt (check, was in der Datei version.json steht) und installiert diese. Dazu muss der Arduino noch zurückgeben, welche Version er hat.

Falls es noch gar nicht geflash ist, so muss dies auch geschehen.

Closed 2022-09-15.

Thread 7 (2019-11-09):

Einbau und Auslese eines Temp.- und Feuchtesensors

pbotte, 2019-11-09:

pbotte, 2019-12-08:
Dies sollte alternativ extern erledigt werden, einmal für eine ganze Gruppe von Waagen. Dafür würden sich z.B. Zigbee Sensoren von Aqara eignen.

pbotte, 2022-06-12:
Im neuesten Design ist ein Temp.-Sensor bei jeder Waage enthalten.

Closed 2022-06-12.

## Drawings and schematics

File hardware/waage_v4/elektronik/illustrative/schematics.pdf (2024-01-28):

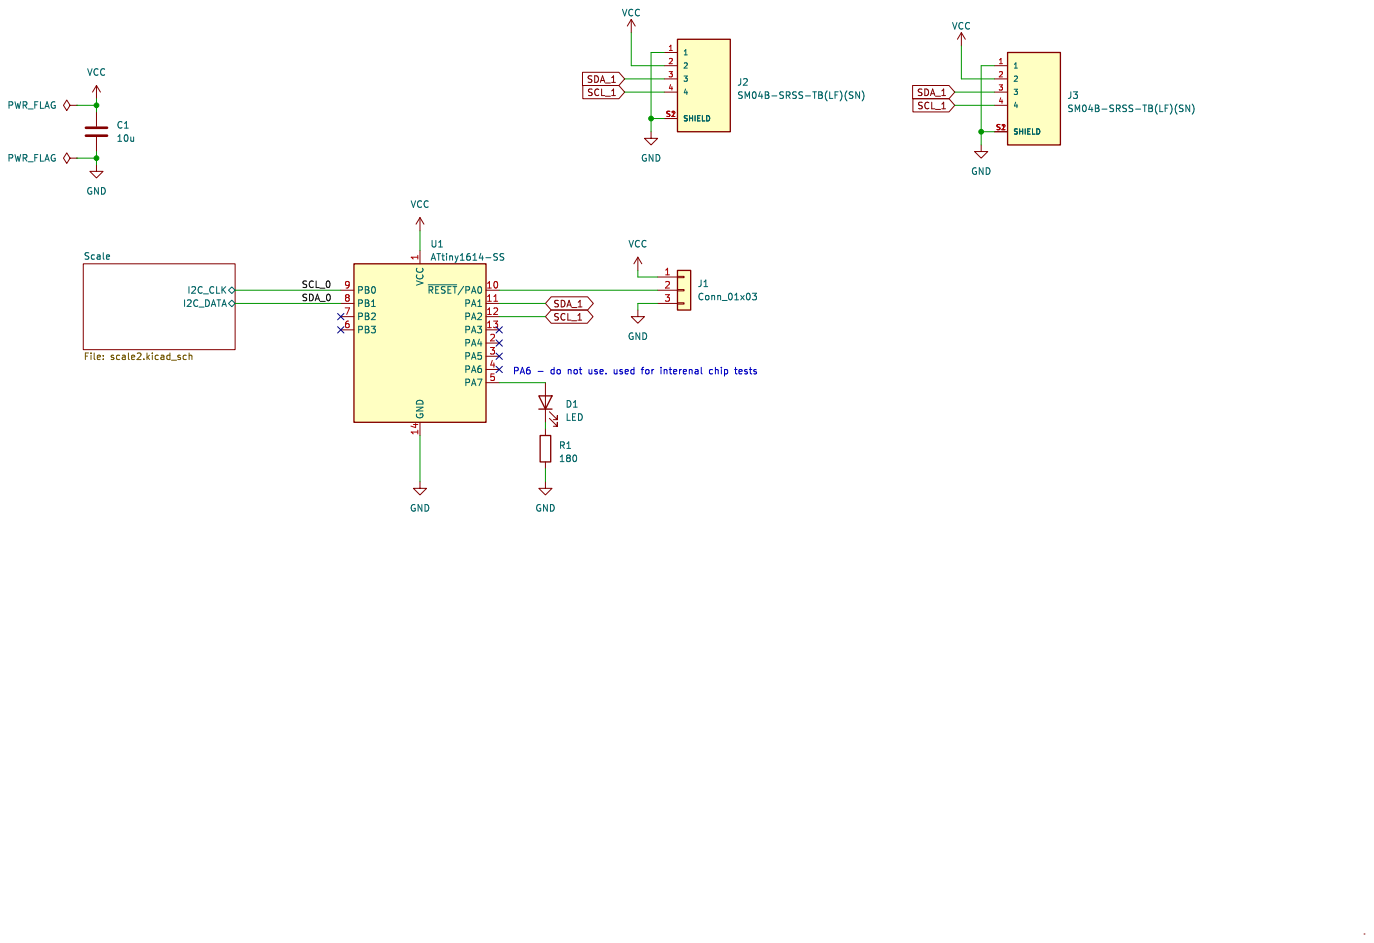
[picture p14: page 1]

1 ~{RESET}/PA010 PA1 11 PA2 12 PA3 13 GND 14 PA4 2 PA5 3 PA6 4 PA7 5 PB3 6 PB2 7 PB1 8 PB0 9 U1ATtiny1614-SS GND

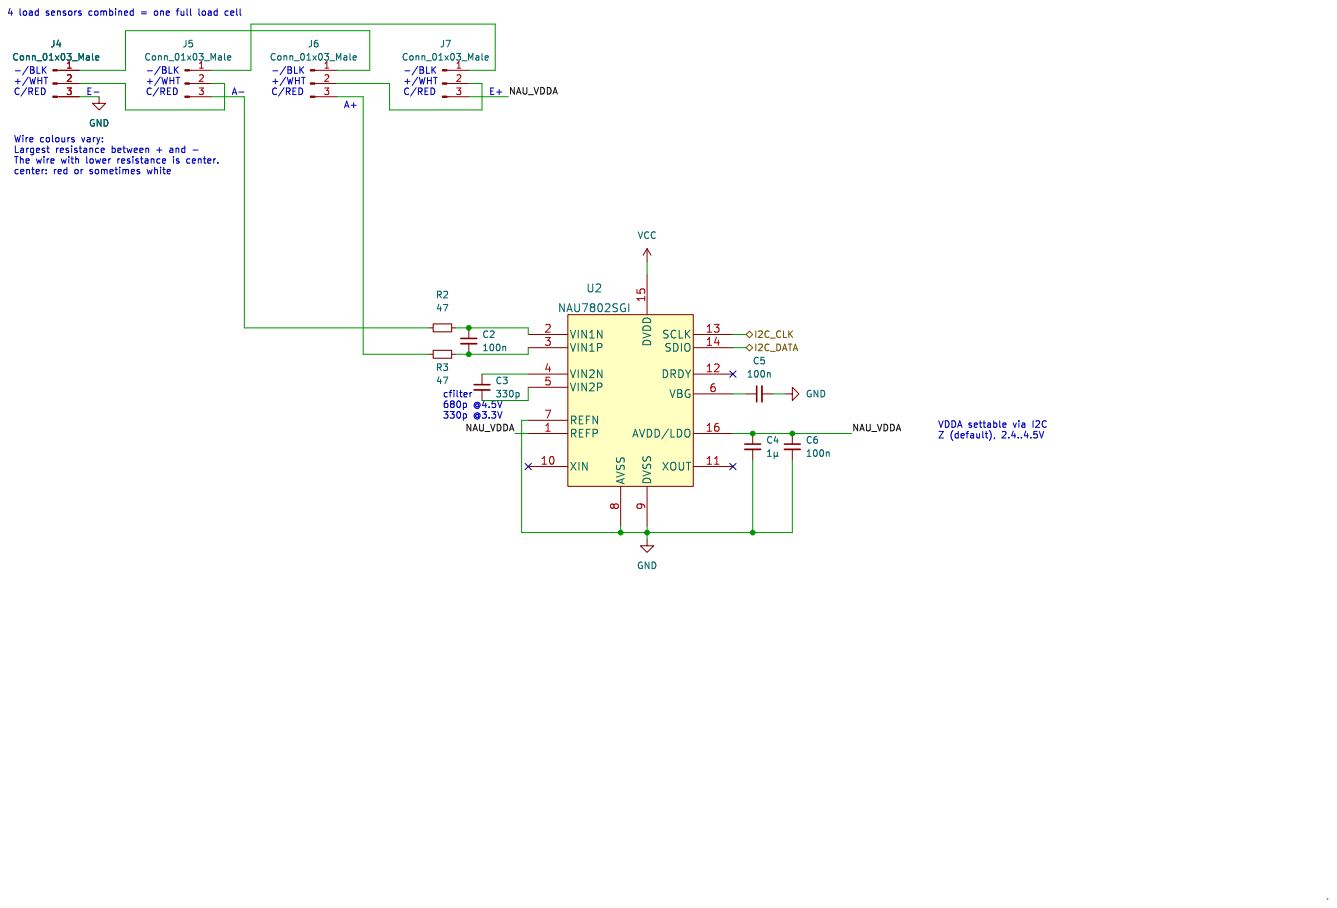
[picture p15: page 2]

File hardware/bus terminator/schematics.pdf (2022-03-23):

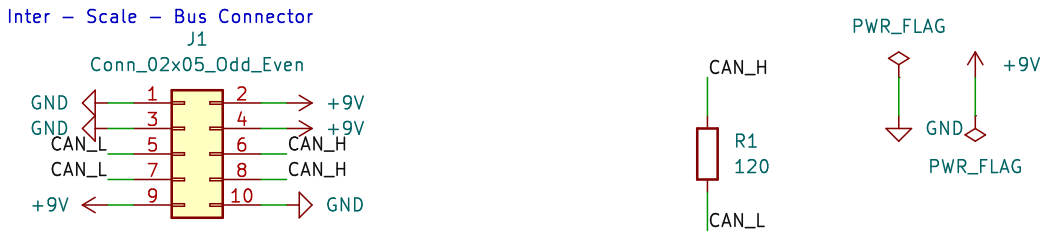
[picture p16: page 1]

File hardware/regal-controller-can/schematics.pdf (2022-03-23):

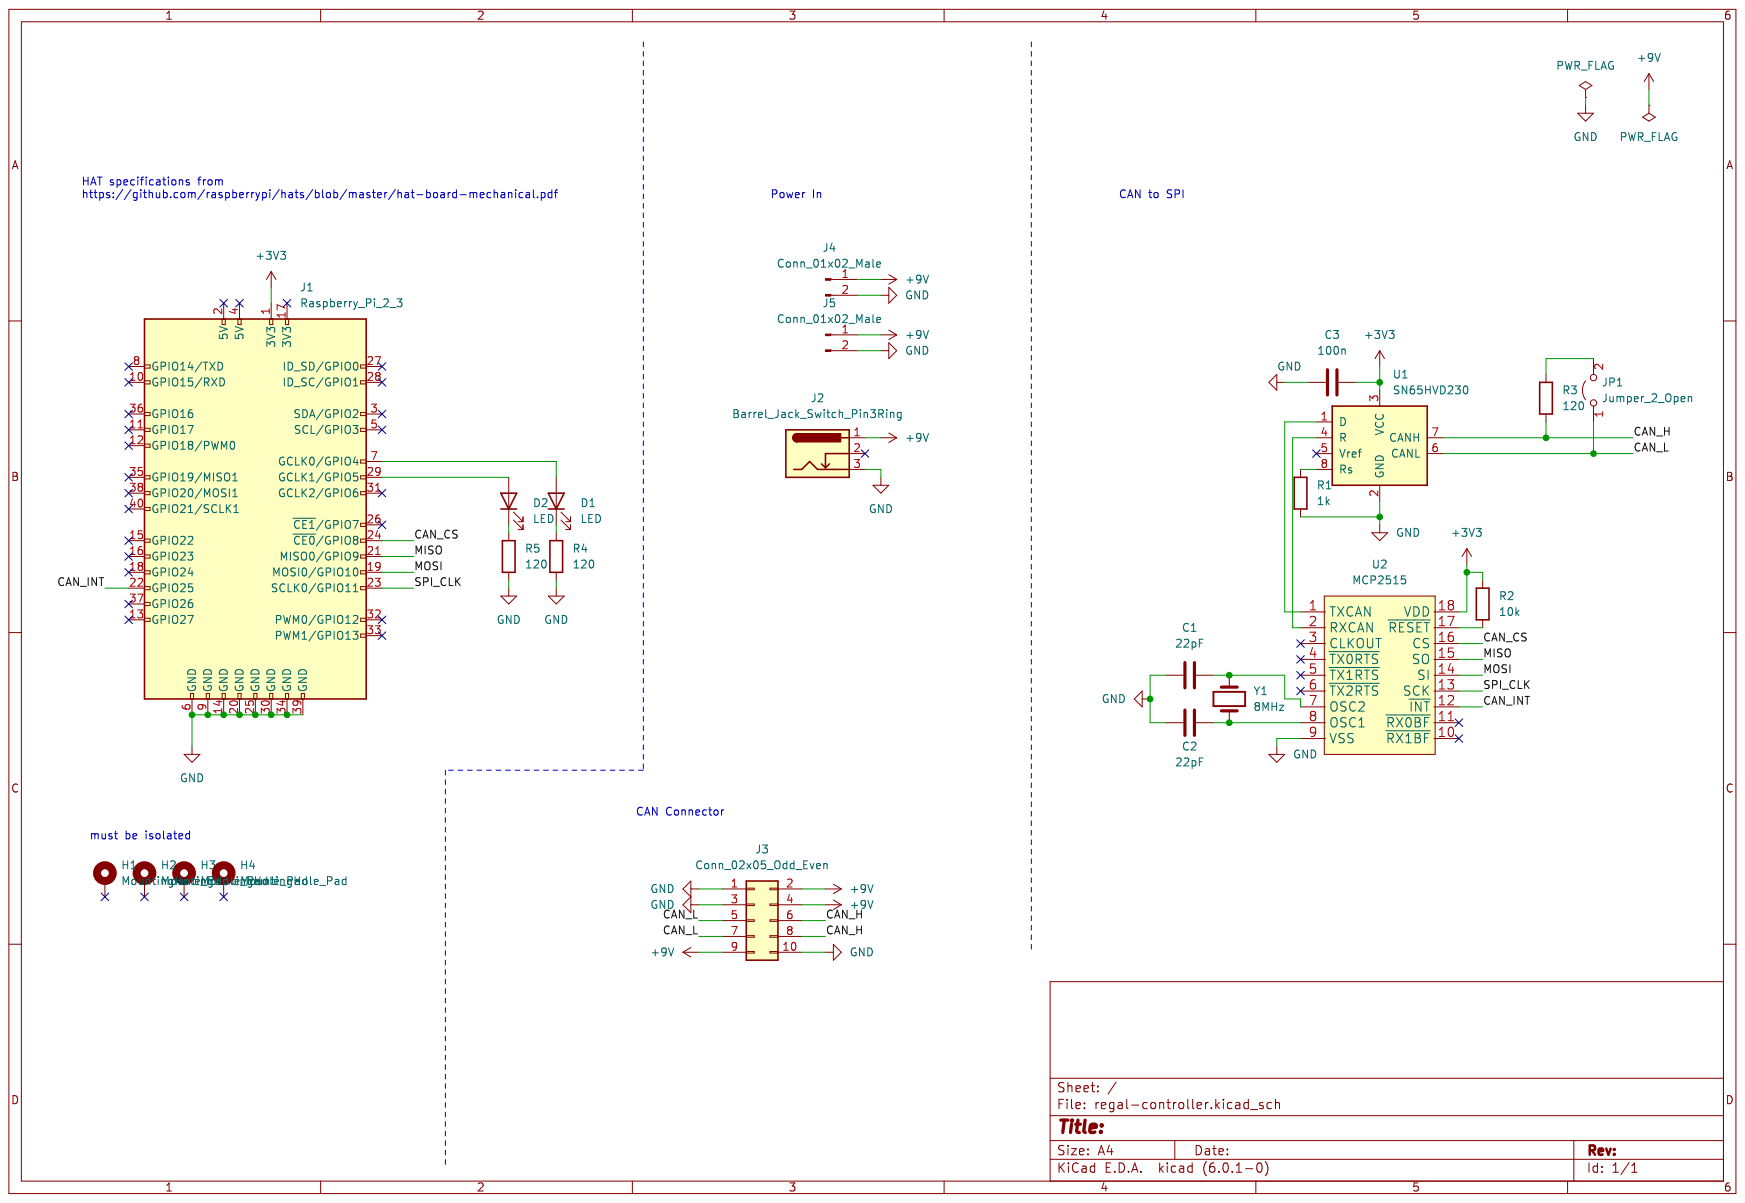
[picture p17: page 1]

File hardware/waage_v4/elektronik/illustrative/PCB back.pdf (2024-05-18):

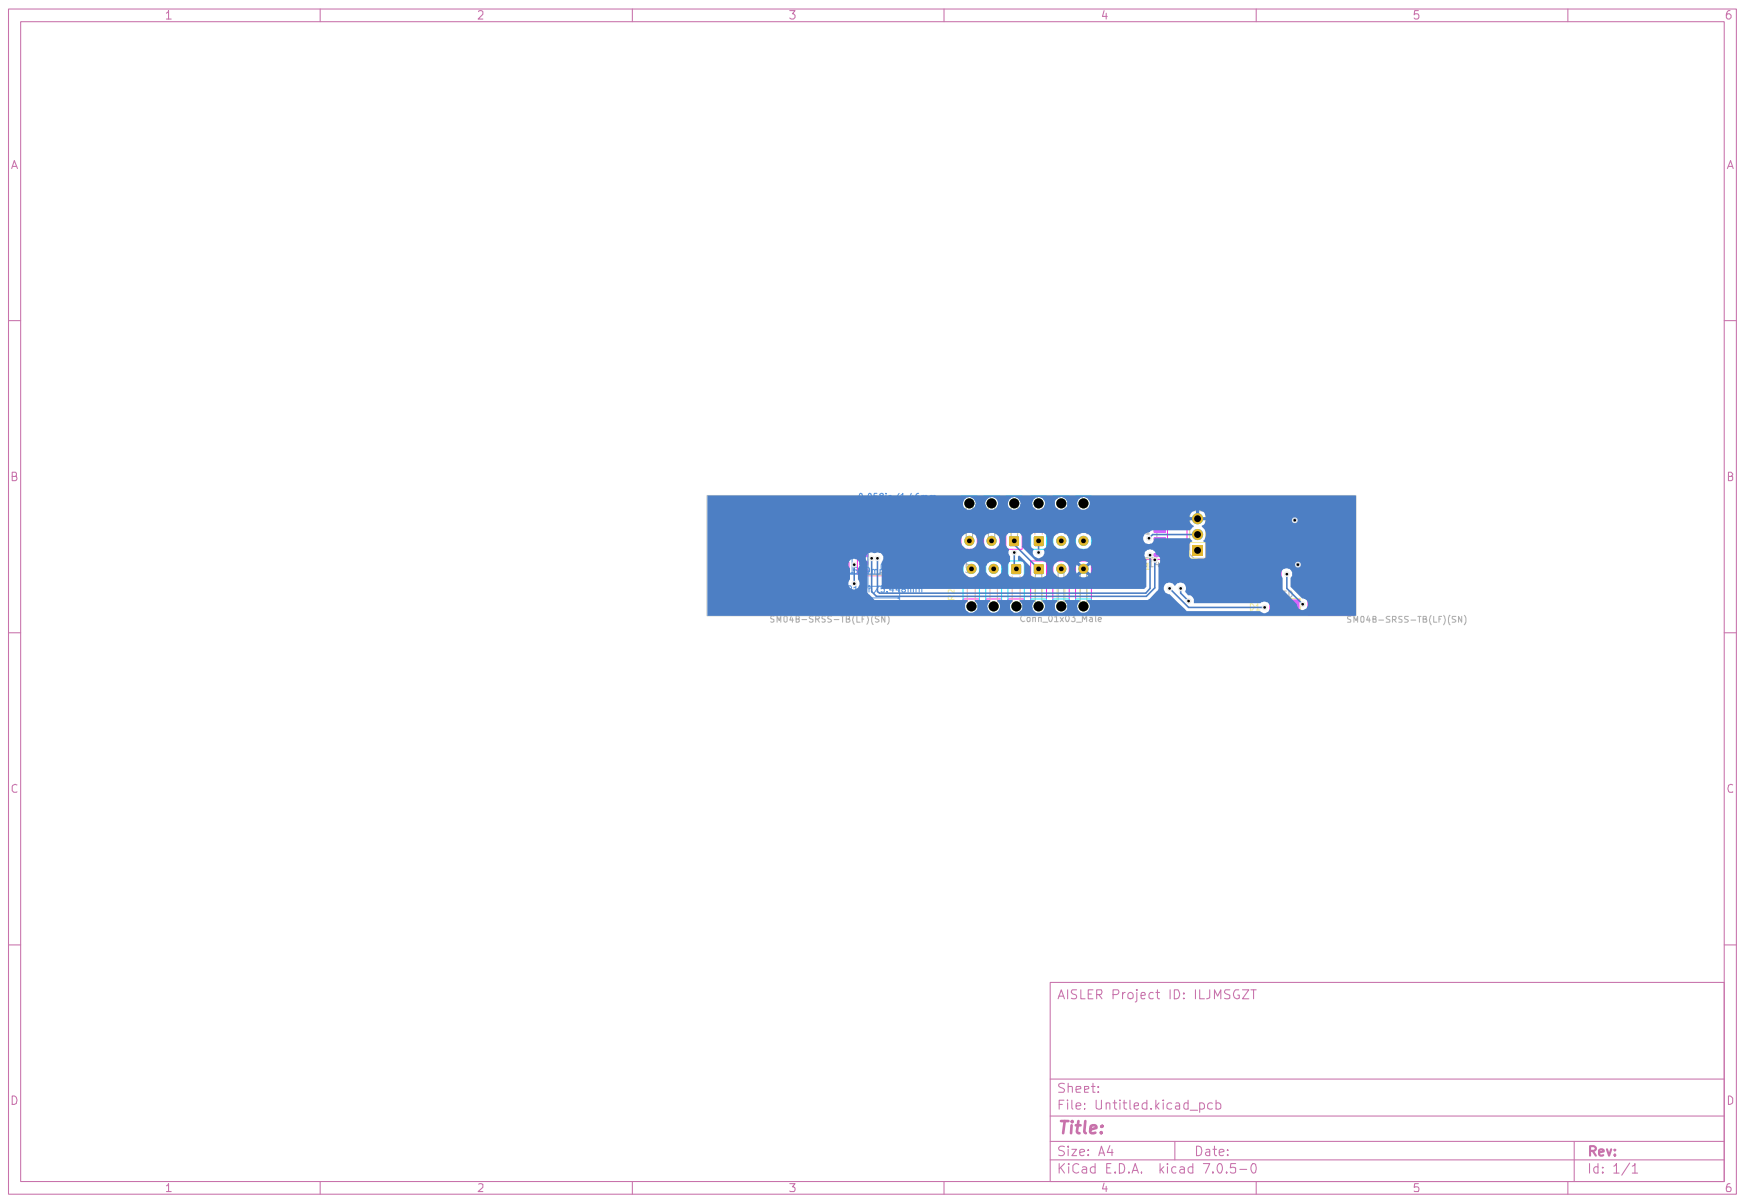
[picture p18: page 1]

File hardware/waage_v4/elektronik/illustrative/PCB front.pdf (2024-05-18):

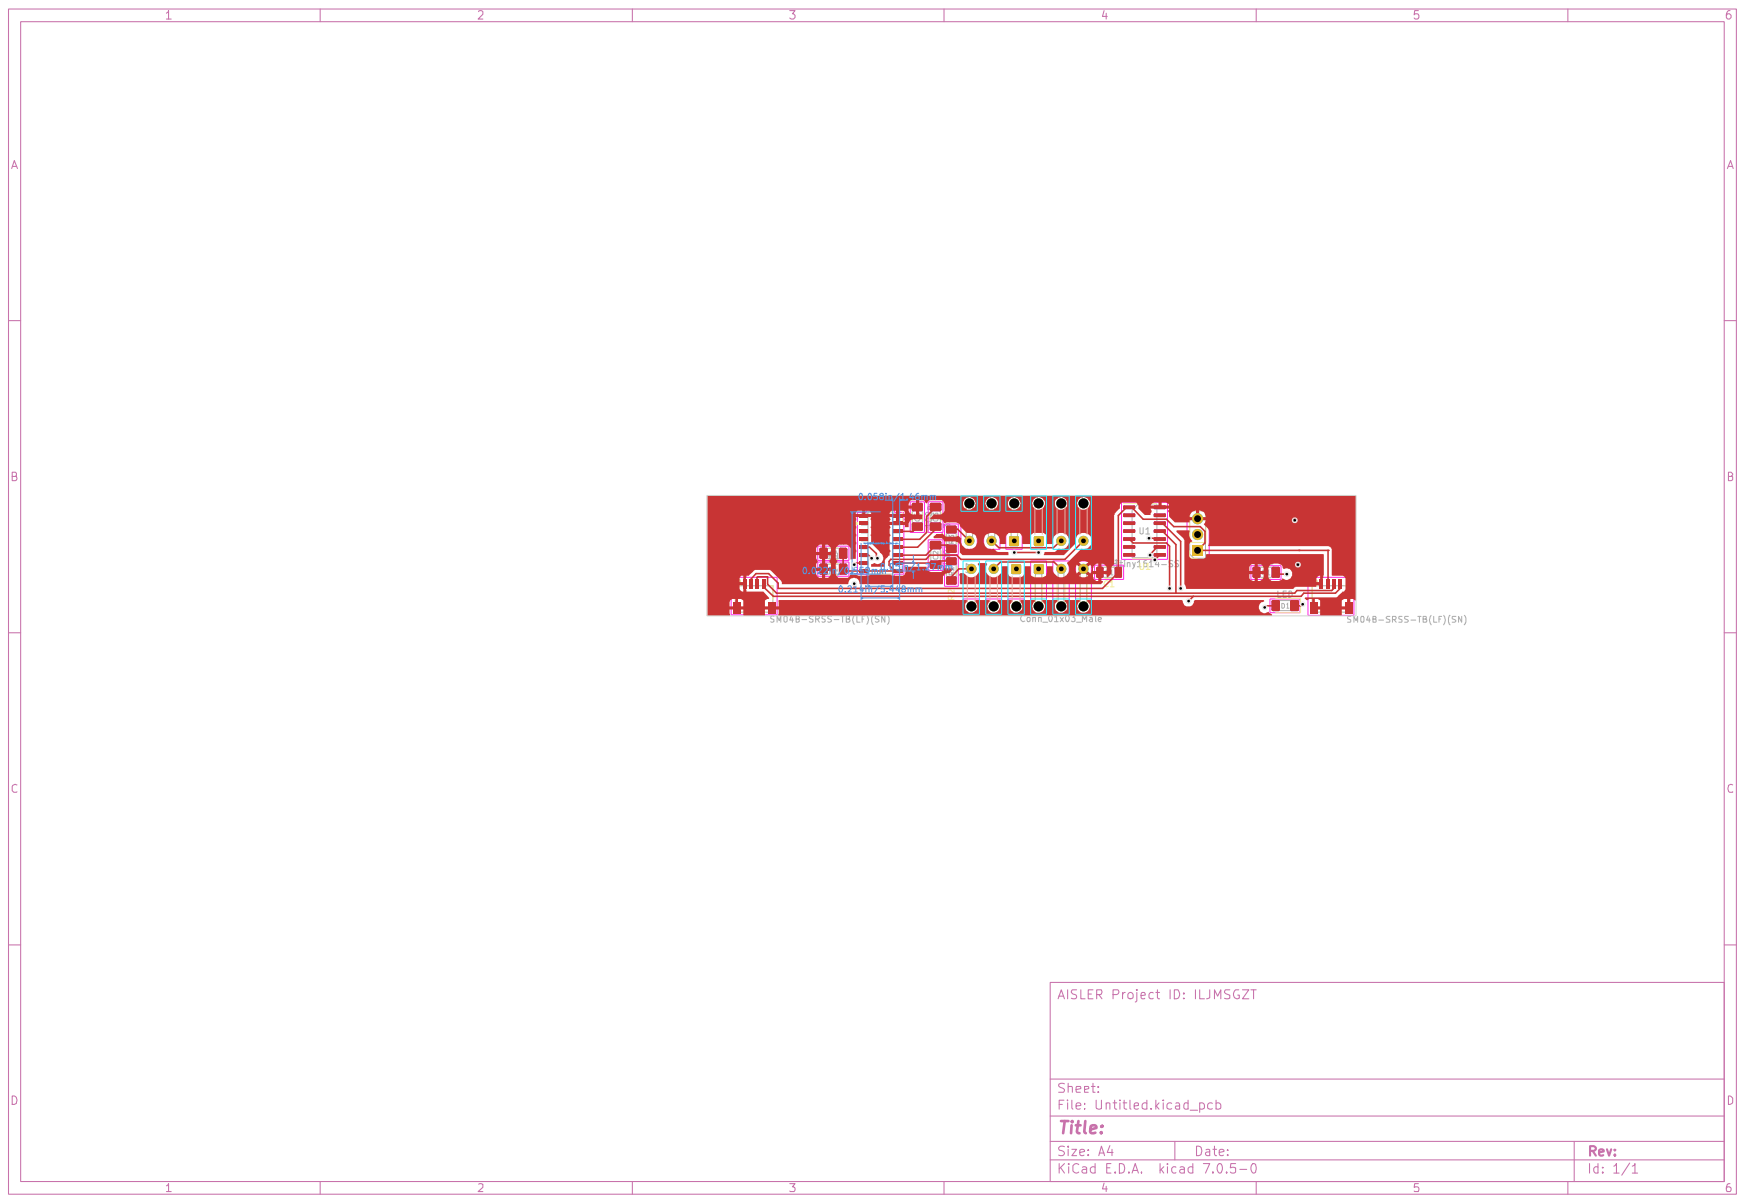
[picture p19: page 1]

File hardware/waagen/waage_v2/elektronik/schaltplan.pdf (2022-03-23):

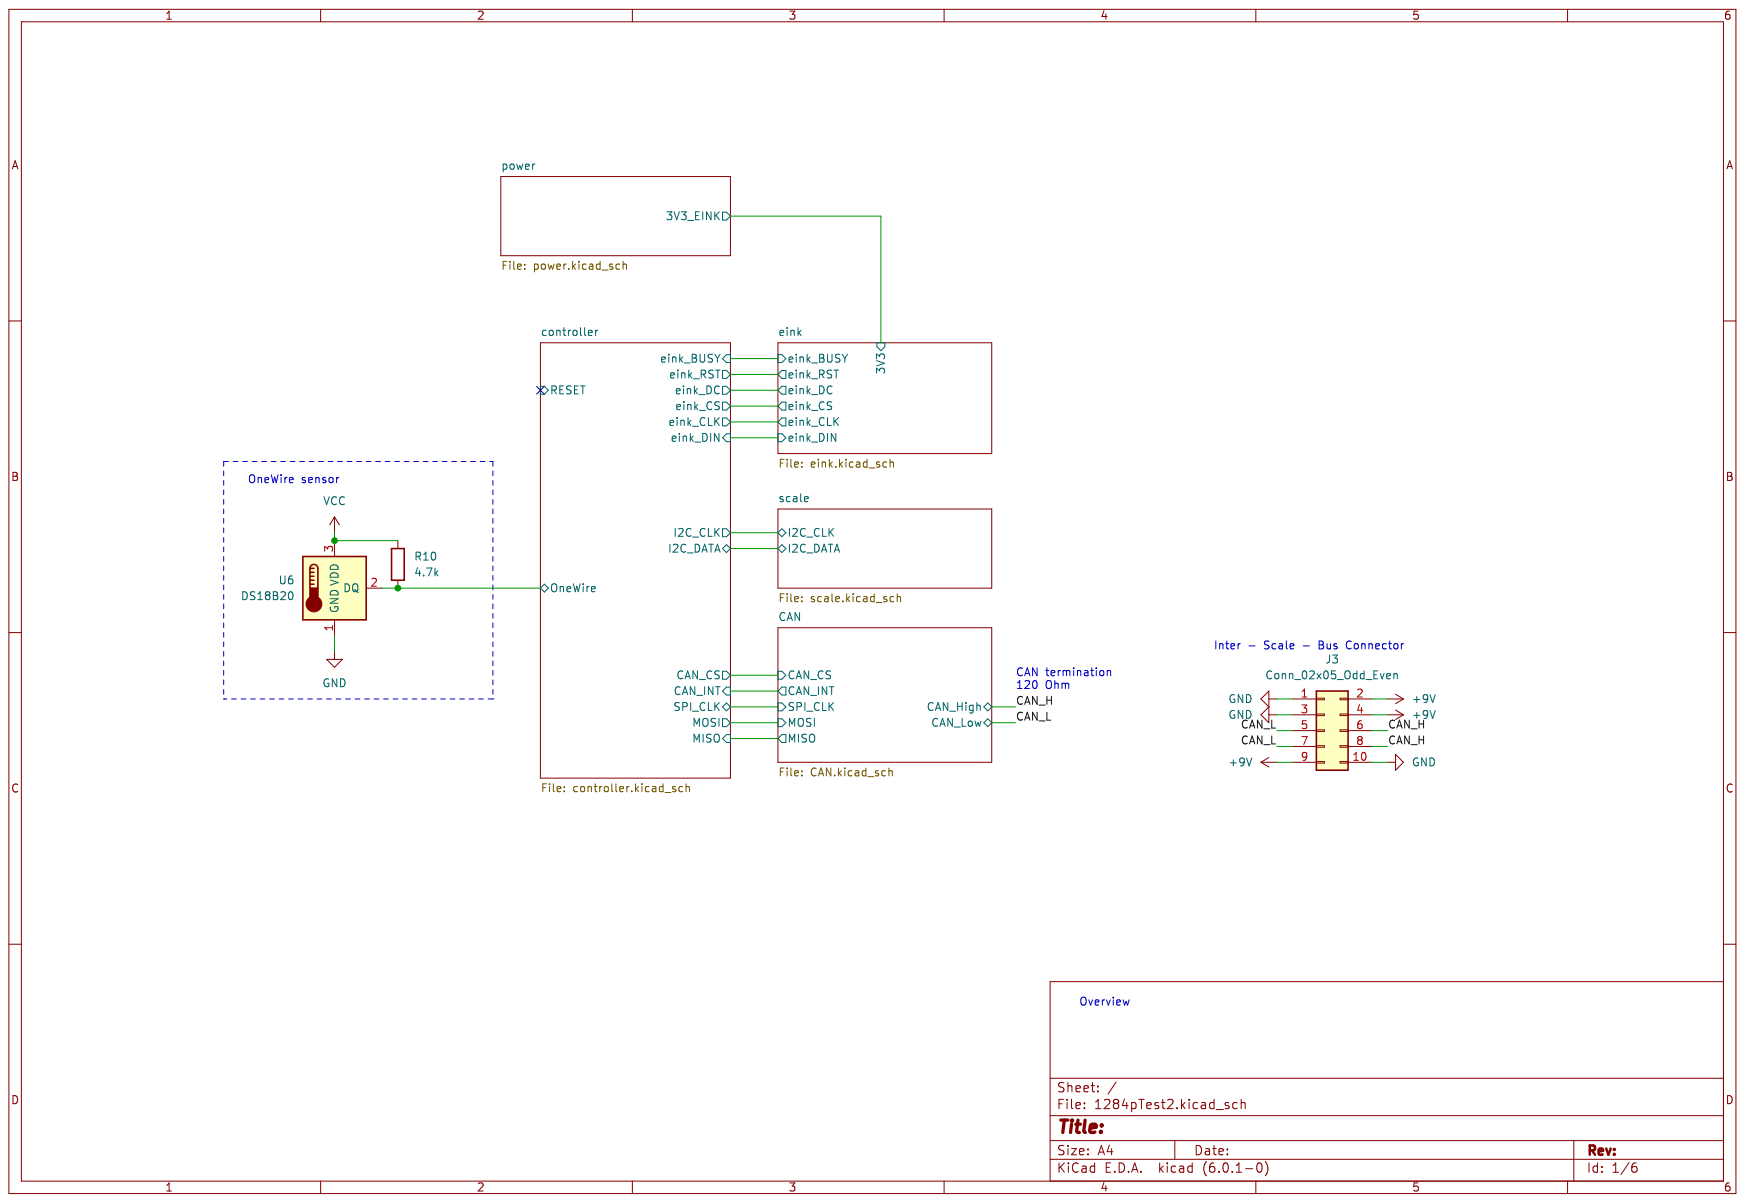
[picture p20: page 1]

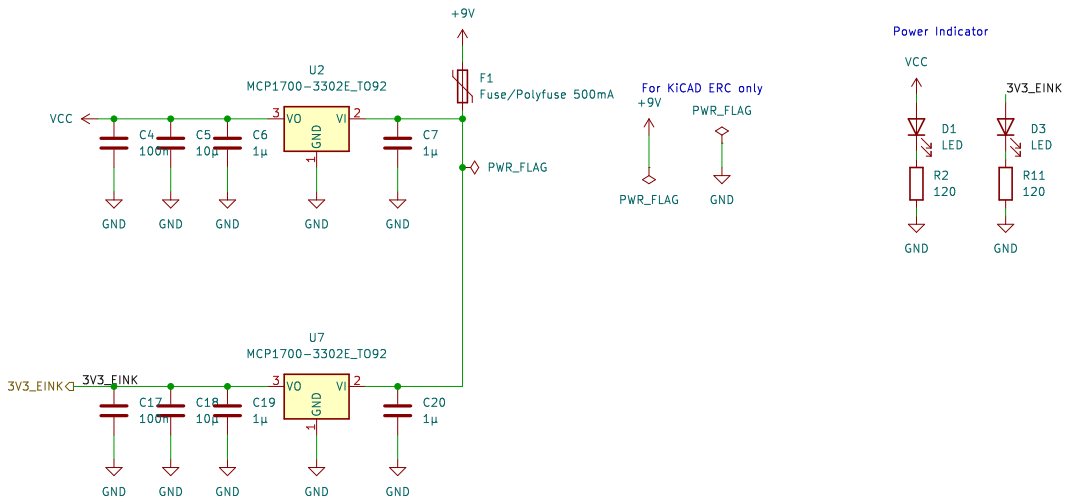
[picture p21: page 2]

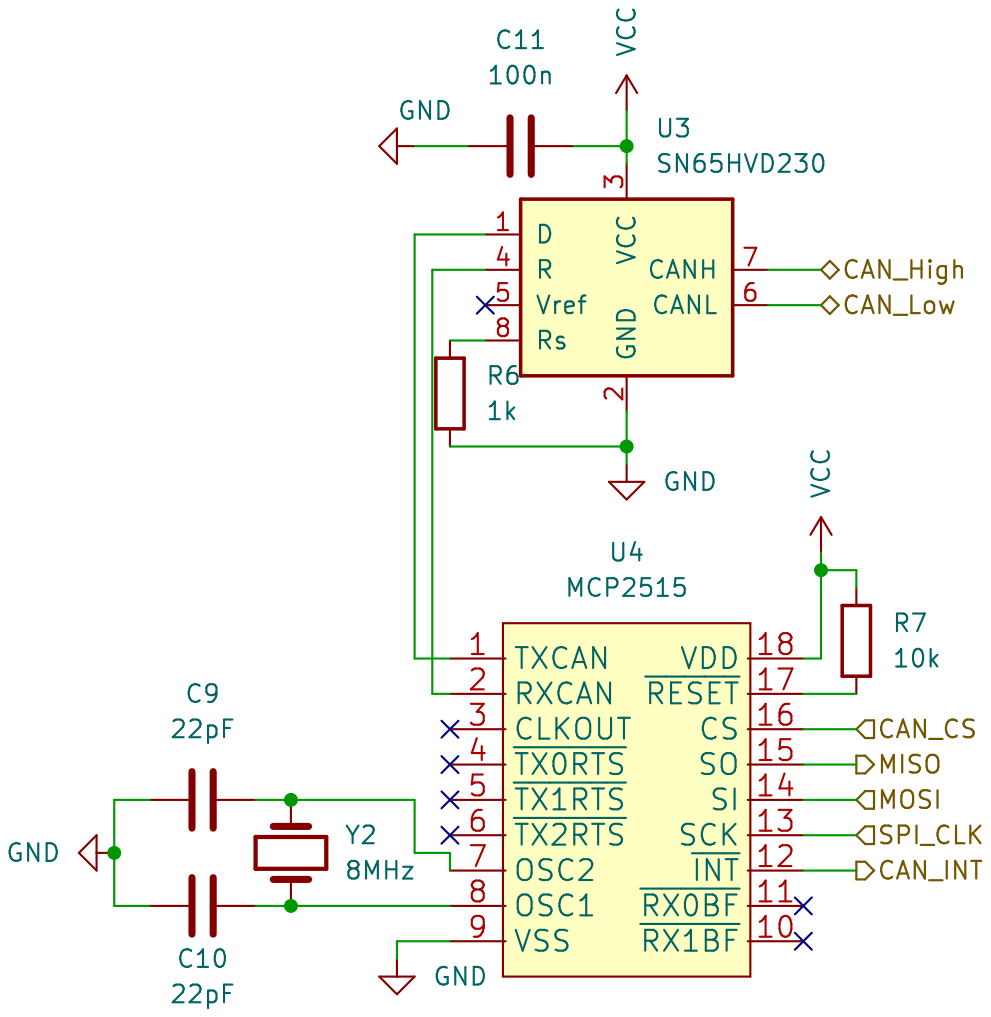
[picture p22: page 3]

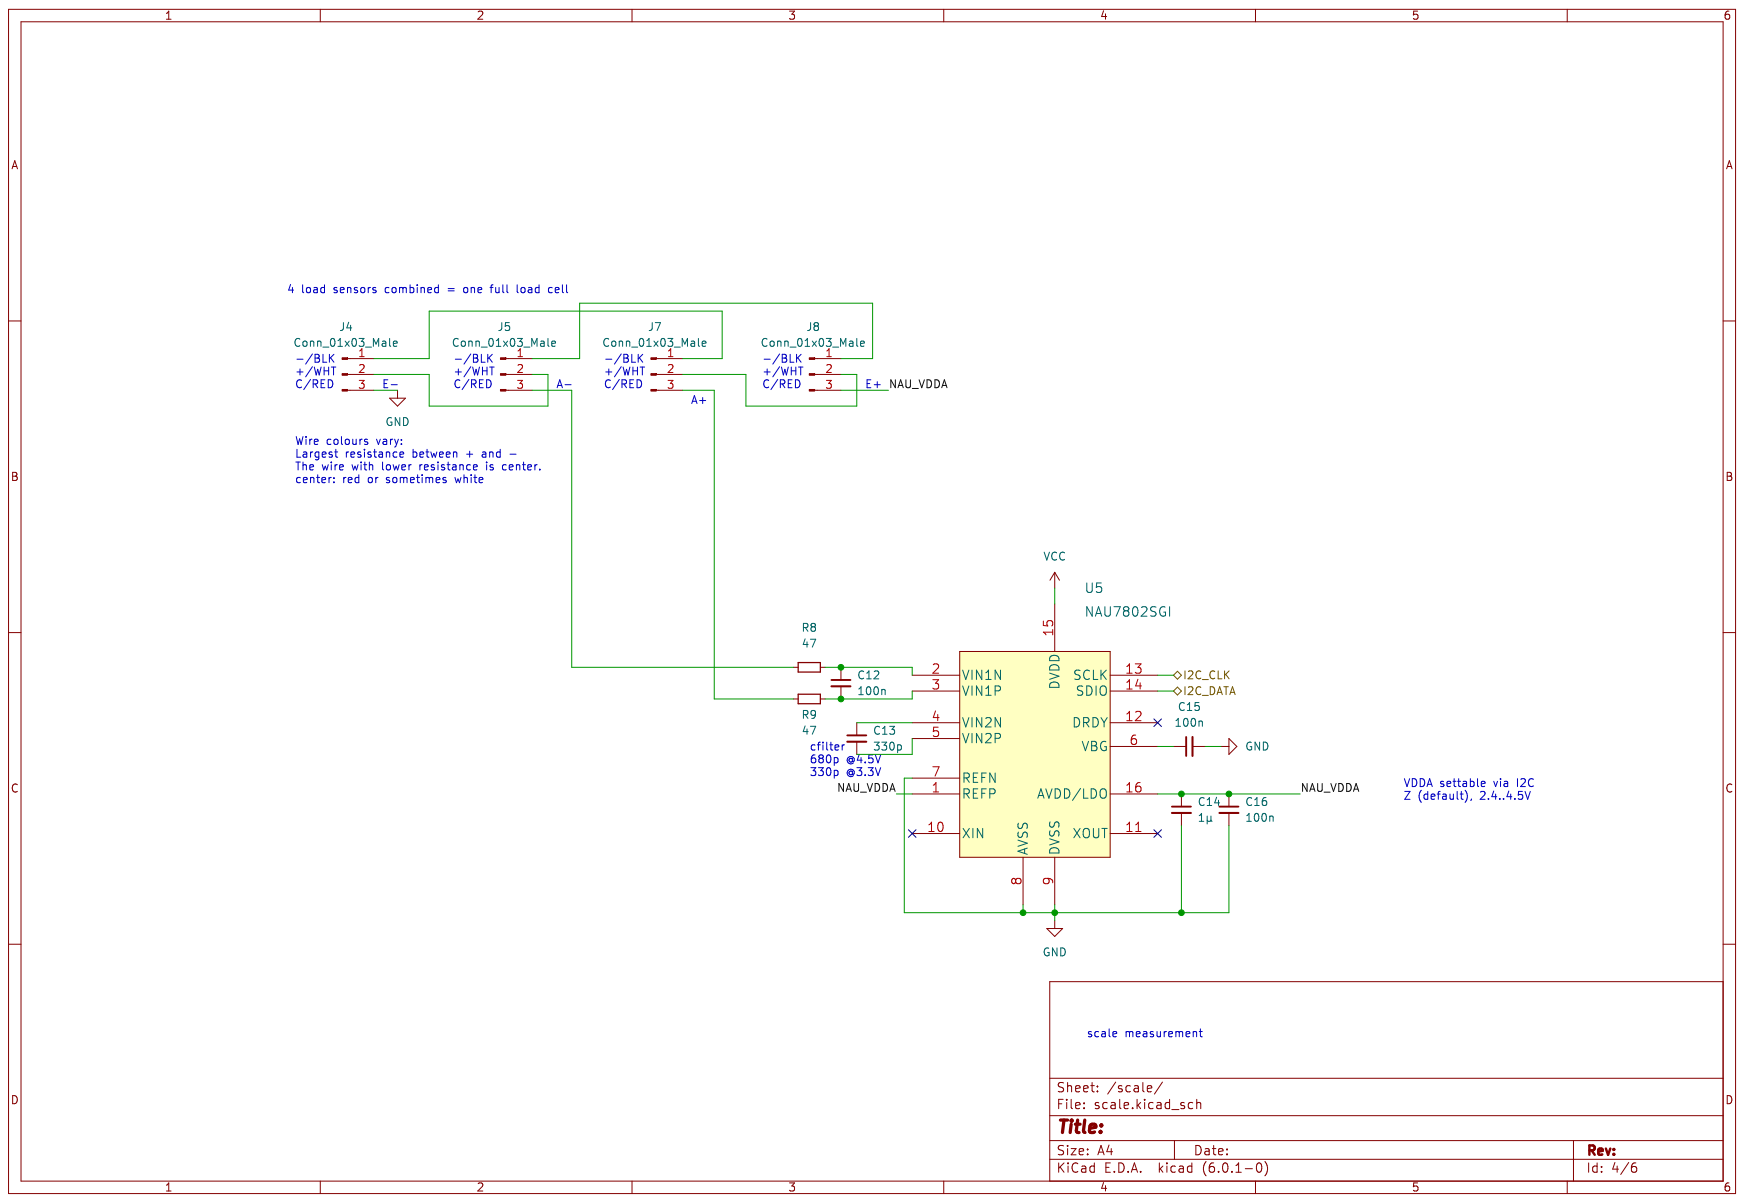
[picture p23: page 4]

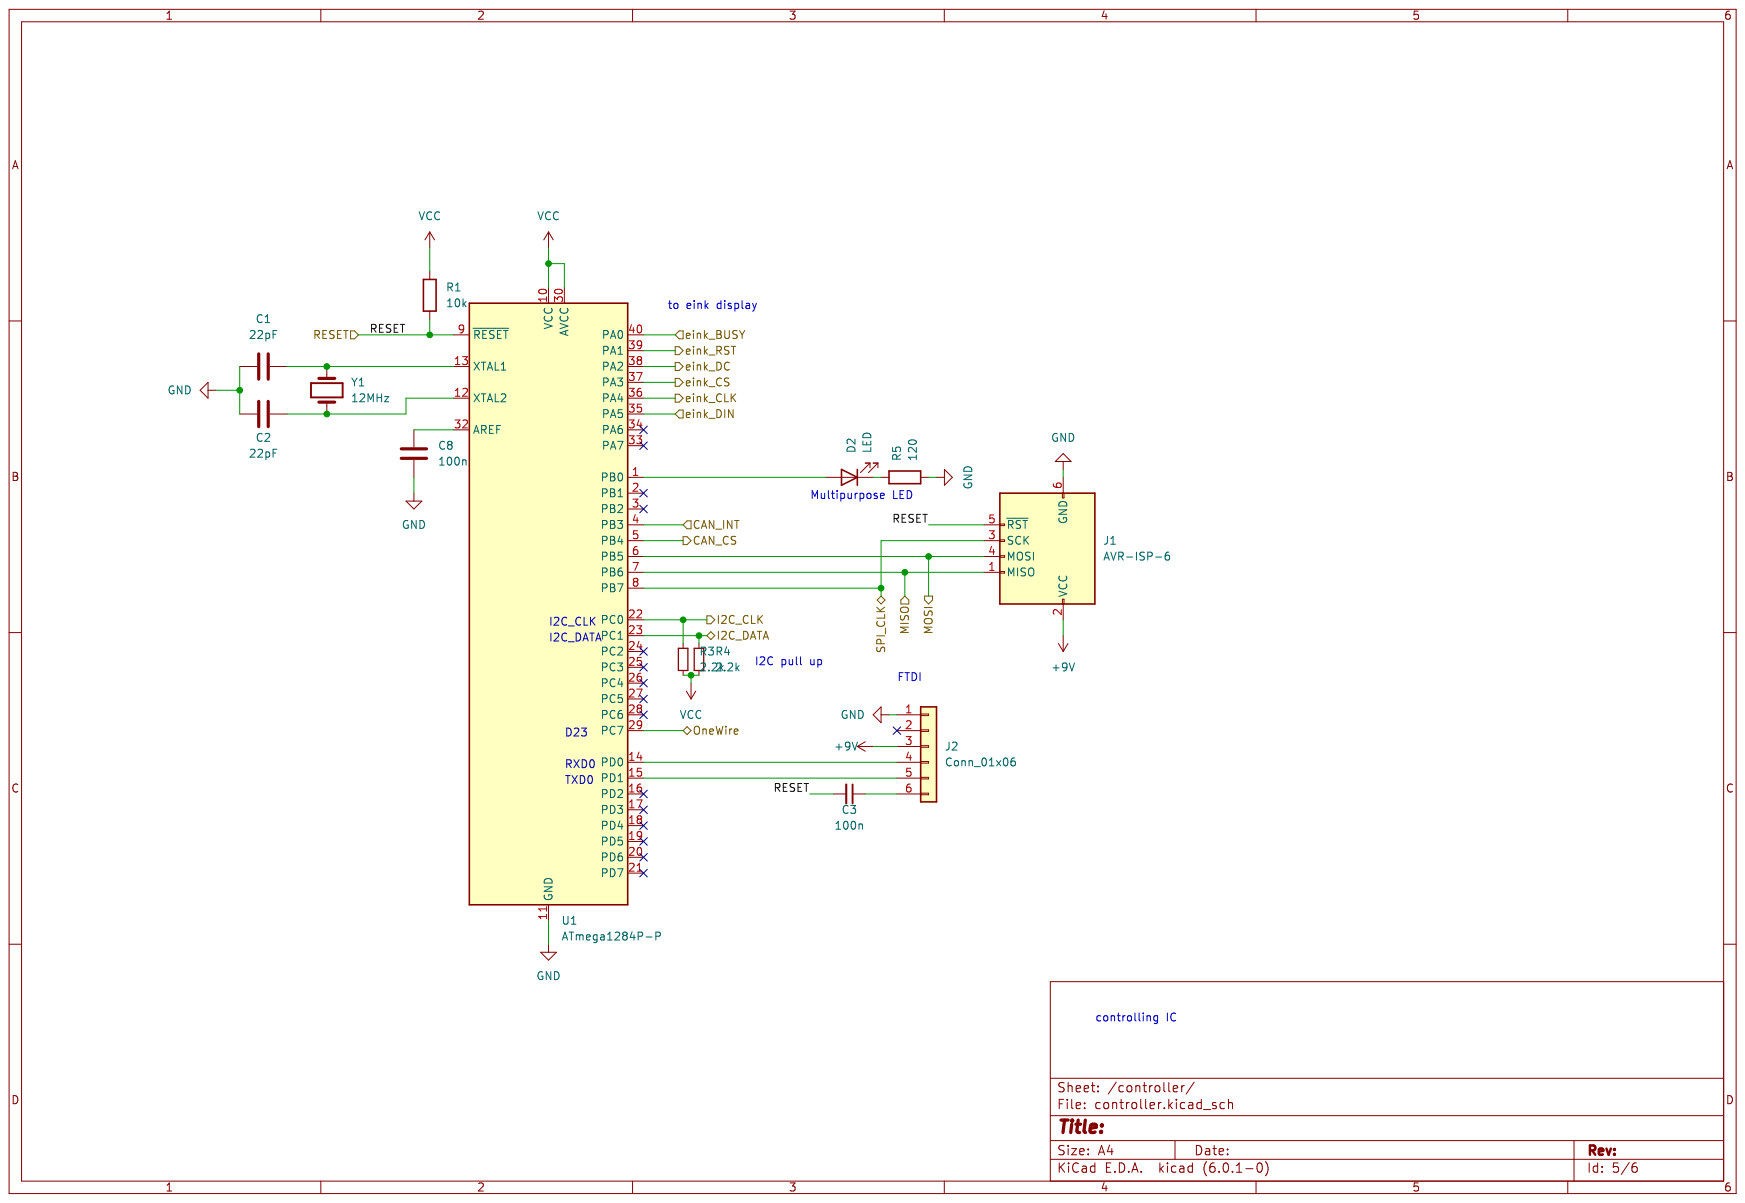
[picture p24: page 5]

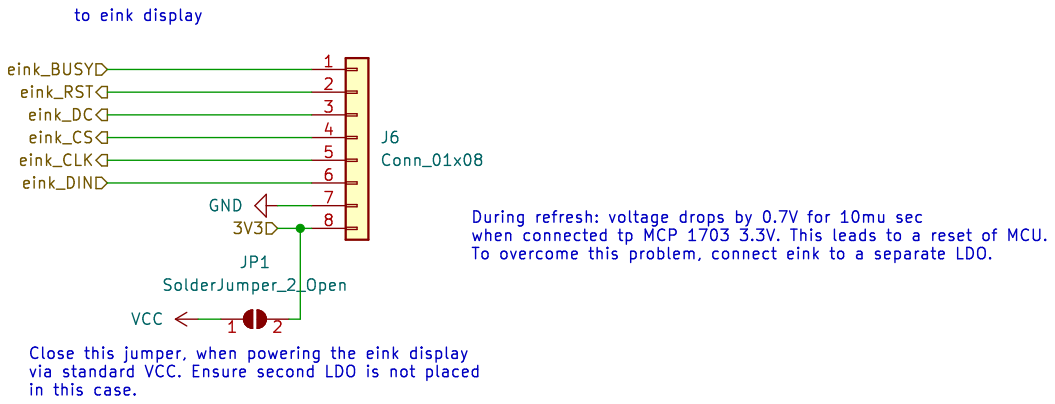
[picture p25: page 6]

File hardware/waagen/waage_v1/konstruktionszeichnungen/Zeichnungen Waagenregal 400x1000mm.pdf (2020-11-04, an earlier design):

6
5

MATERIAL; FINISH; 8x Wägeplatte Alu 5mm; M3 Senkgewinde

UNLESS OTHERWISE SPECIFIED, DIMENSIONS ARE IN MILLIMETERS ANGULAR = ± ° SURFACE FINISH | | NAME | SIGNATURE | DATE

DRAWN | PETER OTTE | | 2020-01-11

CHECKED | | | | TITLE Waagenregal

APPROVED

DO NOT SCALE DRAWING

BREAK ALL SHARP EDGES AND

REMOVE BURRS
FIRST ANGLE PROJECTION

SIZE A3 | DWG NO. | REV. 1

SCALE 1:2 | WEIGHT | SHEET

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


66
55

SHEET; REV.; SCALE A3 DWG NO.; SIZE; 2x Loch für M5; 2x Loch für M8; 7x Aussparung für Trenner (Breite 2.0mm, Dicke Trenner 2.0mm); 2x Längsbalken Alu-Winkel 60x40x5 5; 20⁴²⁵

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

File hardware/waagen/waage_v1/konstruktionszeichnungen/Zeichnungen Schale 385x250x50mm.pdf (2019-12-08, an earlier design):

6
5

MATERIAL; FINISH; SIZE A3; DWG NO.; REV.; SCALE; WEIGHT; SHEET; 1x Wägeschale; Material: VA, 1mm

UNLESS OTHERWISE SPECIFIED, DIMENSIONS ARE IN MILLIMETERS ANGULAR = ± ° SURFACE FINISH | | NAME | SIGNATURE | DATE

DRAWN | PETER OTTE | | 2019-11-22

CHECKED | | | | TITLE Schale aus VA

APPROVED

DO NOT SCALE DRAWING

BREAK ALL SHARP EDGES AND

REMOVE BURRS
FIRST ANGLE PROJECTION

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

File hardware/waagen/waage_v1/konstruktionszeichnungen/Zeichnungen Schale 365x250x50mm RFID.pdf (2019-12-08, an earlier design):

6
5

MATERIAL; FINISH; SIZE A3; DWG NO.; REV.; SCALE; WEIGHT; SHEET; 1x Wägeschale; Material: VA, 1mm

UNLESS OTHERWISE SPECIFIED, DIMENSIONS ARE IN MILLIMETERS ANGULAR = ± ° SURFACE FINISH | | NAME | SIGNATURE | DATE

DRAWN | PETER OTTE | | 2019-11-22

CHECKED | | | | TITLE Schale aus VA

APPROVED

DO NOT SCALE DRAWING

BREAK ALL SHARP EDGES AND

REMOVE BURRS
FIRST ANGLE PROJECTION

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

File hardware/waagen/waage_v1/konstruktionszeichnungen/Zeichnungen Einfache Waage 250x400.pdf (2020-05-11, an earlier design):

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

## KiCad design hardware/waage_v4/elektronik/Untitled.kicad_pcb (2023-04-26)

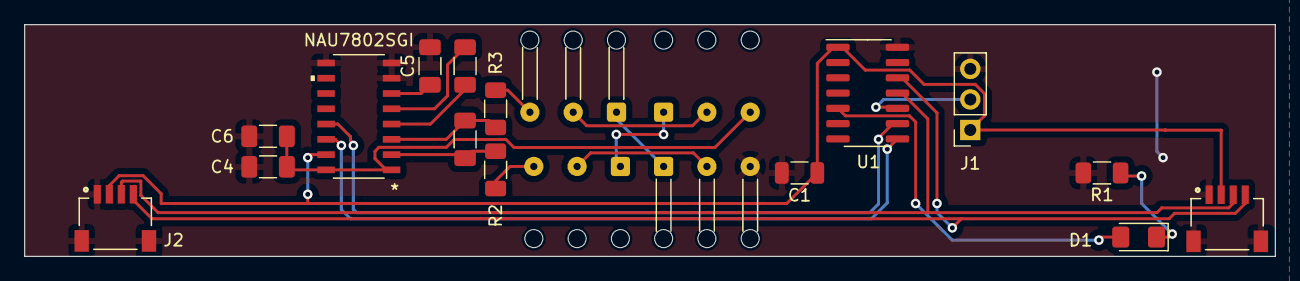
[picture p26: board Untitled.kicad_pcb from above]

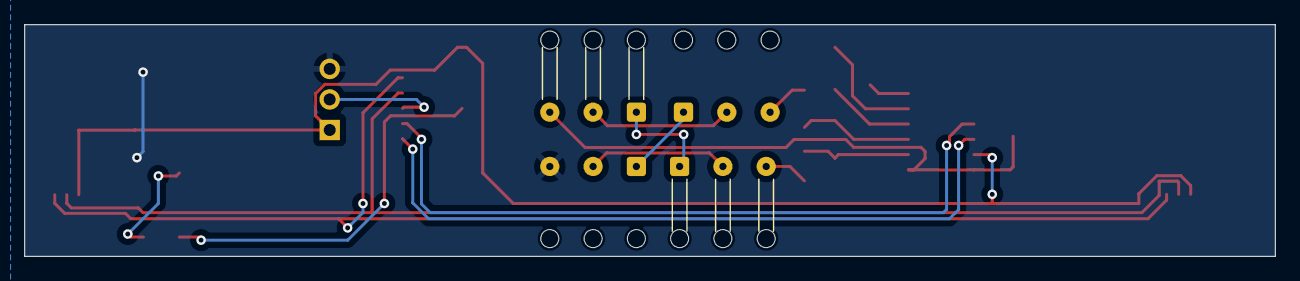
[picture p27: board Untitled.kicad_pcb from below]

Board: 2 copper layers, 104.0 x 19.3 mm, 19 parts (2 on the bottom side), 21 nets.

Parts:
C1: 10u; C_1206_3216Metric
C2, C5, C6: 100n; C_1206_3216Metric_Pad1.33x1.80mm_HandSolder
C3: 330p; C_1206_3216Metric_Pad1.33x1.80mm_HandSolder
C4: 1µ; C_1206_3216Metric_Pad1.33x1.80mm_HandSolder
D1: LED; LED_1206_3216Metric_Pad1.42x1.75mm_HandSolder
J1: Conn_01x03; PinSocket_1x03_P2.54mm_Vertical
J2, J3: SM04B-SRSS-TB(LF)(SN); JST_SM04B-SRSS-TB(LF)(SN)
J4, J5, J6, J7: Conn_01x03_Male; SolderWire-0.1sqmm_1x03_P3.6mm_D0.4mm_OD1mm_Relief
R1: 180; R_1206_3216Metric_Pad1.30x1.75mm_HandSolder
R2, R3: 47; R_1206_3216Metric_Pad1.30x1.75mm_HandSolder
U1: ATtiny1614-SS; SOIC-14_3.9x8.7mm_P1.27mm
U2: NAU7802SGI

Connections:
/SCL_0: U1.9 (PB0), U2.13 (SCLK)
/SDA_0: U1.8 (PB1), U2.14 (SDIO)
/Scale/NAU_VDDA: C4.1, C6.1, J7.3, U2.1 (REFP), U2.16 (AVDD/LDO)
GND: C1.2, C4.2, C5.2, C6.2, J1.3, J2.1, J2.S1 (SHIELD), J2.S2 (SHIELD), J3.1, J3.S1 (SHIELD), J3.S2 (SHIELD), J4.3, R1.2, U1.14 (GND), U2.7 (REFN), U2.8 (AVSS), U2.9 (DVSS)
unnamed: D1.2 (A), U1.5 (PA7)
unnamed: D1.1 (K), R1.1
unnamed: J1.2, U1.10 (~RESET/PA0)
unnamed: J4.1, J6.1
unnamed: J4.2, J5.2
unnamed: J5.1, J7.1
unnamed: J5.3, R2.1
unnamed: J6.2, J7.2
unnamed: J6.3, R3.1
unnamed: C5.1, U2.6 (VBG)
unnamed: C2.1, R2.2, U2.2 (VIN1N)
unnamed: C2.2, R3.2, U2.3 (VIN1P)
unnamed: C3.1, U2.4 (VIN2N)
unnamed: C3.2, U2.5 (VIN2P)
SCL_1: J2.4, J3.4, U1.12 (PA2)
SDA_1: J2.3, J3.3, U1.11 (PA1)
VCC: C1.1, J1.1, J2.2, J3.2, U1.1 (VCC), U2.15 (DVDD)

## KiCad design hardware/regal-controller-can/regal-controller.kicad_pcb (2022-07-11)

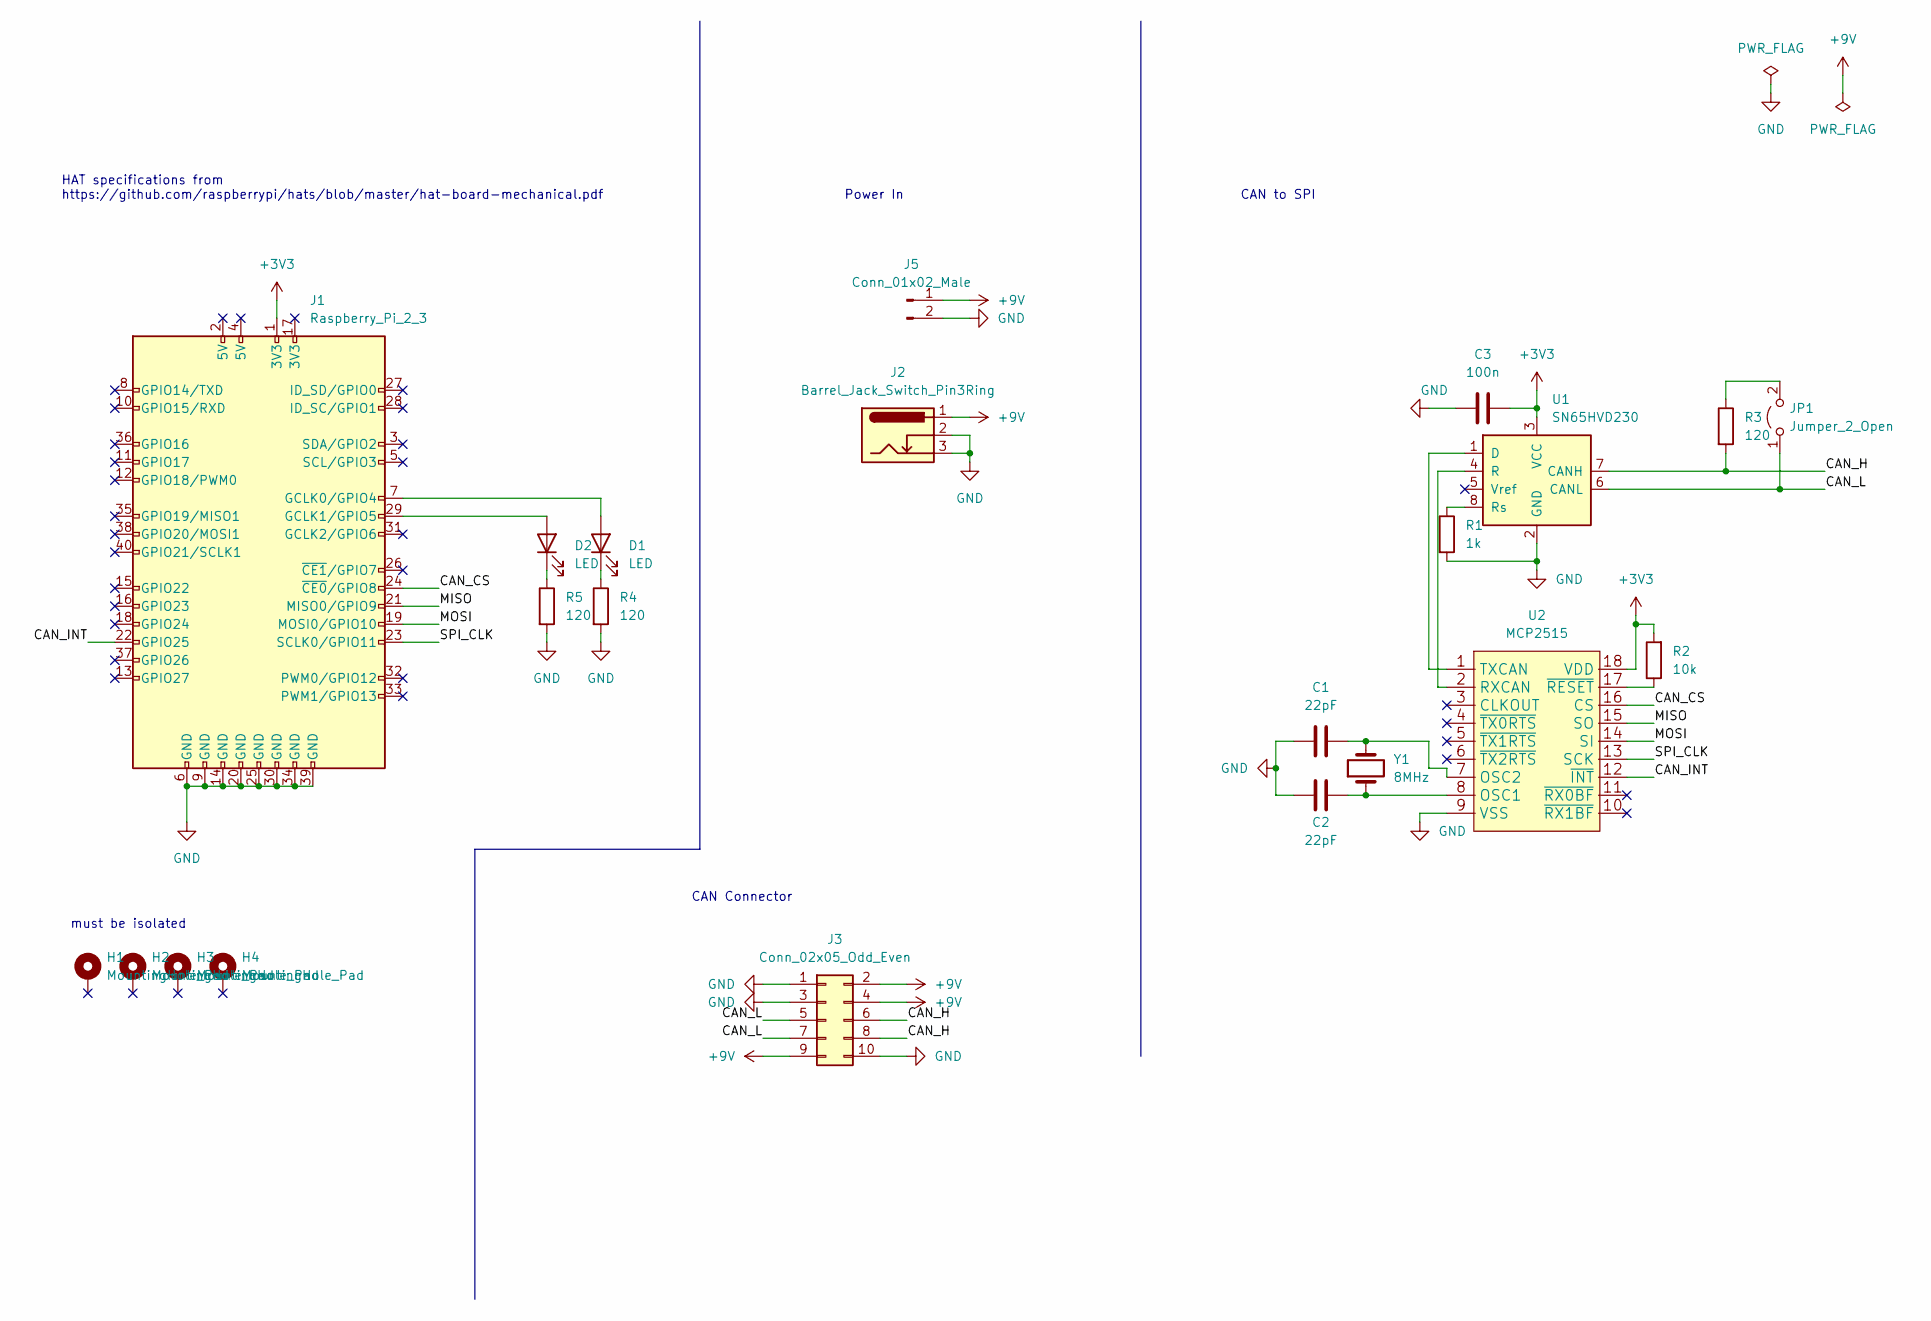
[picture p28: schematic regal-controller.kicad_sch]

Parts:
C1, C2: 22pF; C_1206_3216Metric_Pad1.33x1.80mm_HandSolder
C3: 100n; C_1206_3216Metric_Pad1.33x1.80mm_HandSolder
D1, D2: LED; LED_1206_3216Metric_Pad1.42x1.75mm_HandSolder
H1, H2, H3, H4: MountingHole_Pad; MountingHole_2.7mm_M2.5_Pad_TopBottom
J1: Raspberry_Pi_2_3; PinSocket_2x20_P2.54mm_Vertical
J2: Barrel_Jack_Switch_Pin3Ring; BarrelJack_Horizontal
J3: Conn_02x05_Odd_Even; PinSocket_2x05_P2.54mm_Horizontal
J5: Conn_01x02_Male; PinHeader_1x02_P2.54mm_Vertical
JP1: Jumper_2_Open; TestPoint_2Pads_Pitch2.54mm_Drill0.8mm
R1: 1k; R_1206_3216Metric_Pad1.30x1.75mm_HandSolder
R2: 10k; R_1206_3216Metric_Pad1.30x1.75mm_HandSolder
R3, R4, R5: 120; R_1206_3216Metric_Pad1.30x1.75mm_HandSolder
U1: SN65HVD230; SOIC-8_3.9x4.9mm_P1.27mm
U2: MCP2515; DIP-18_W7.62mm_LongPads
Y1: 8MHz; Crystal_SMD_HC49-SD_HandSoldering

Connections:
+3V3: C3.2, J1.1 (3V3), R2.2, U1.3 (VCC), U2.18 (VDD)
+9V: J2.1, J3.2, J3.4, J3.9, J5.1
/CAN_CS: J1.24 (~CE0/GPIO8), U2.16 (CS)
/CAN_H: J3.6, J3.8, R3.2, U1.7 (CANH)
/CAN_INT: J1.22 (GPIO25), U2.12 (~INT)
/CAN_L: J3.5, J3.7, JP1.1 (A), U1.6 (CANL)
/MISO: J1.21 (MISO0/GPIO9), U2.15 (SO)
/MOSI: J1.19 (MOSI0/GPIO10), U2.14 (SI)
/SPI_CLK: J1.23 (SCLK0/GPIO11), U2.13 (SCK)
GND: C1.1, C2.1, C3.1, J1.6 (GND), J1.9 (GND), J1.14 (GND), J1.20 (GND), J1.25 (GND), J1.30 (GND), J1.34 (GND), J1.39 (GND), J2.2, J2.3, J3.1, J3.3, J3.10, J5.2, R1.2, R4.2, R5.2, U1.2 (GND), U2.9 (VSS)
unnamed: C1.2, U2.7 (OSC2), Y1.2
unnamed: C2.2, U2.8 (OSC1), Y1.1
unnamed: D1.1 (K), R4.1
unnamed: D1.2 (A), J1.7 (GCLK0/GPIO4)
unnamed: D2.1 (K), R5.1
unnamed: D2.2 (A), J1.29 (GCLK1/GPIO5)
unnamed: JP1.2 (B), R3.1
unnamed: R1.1, U1.8 (Rs)
unnamed: R2.1, U2.17 (~RESET)
unnamed: U1.1 (D), U2.1 (TXCAN)
unnamed: U1.4 (R), U2.2 (RXCAN)

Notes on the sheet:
CAN to SPI
HAT specifications from https://github.com/raspberrypi/hats/blob/master/hat-board-mechanical.pdf
Power In
must be isolated
CAN Connector

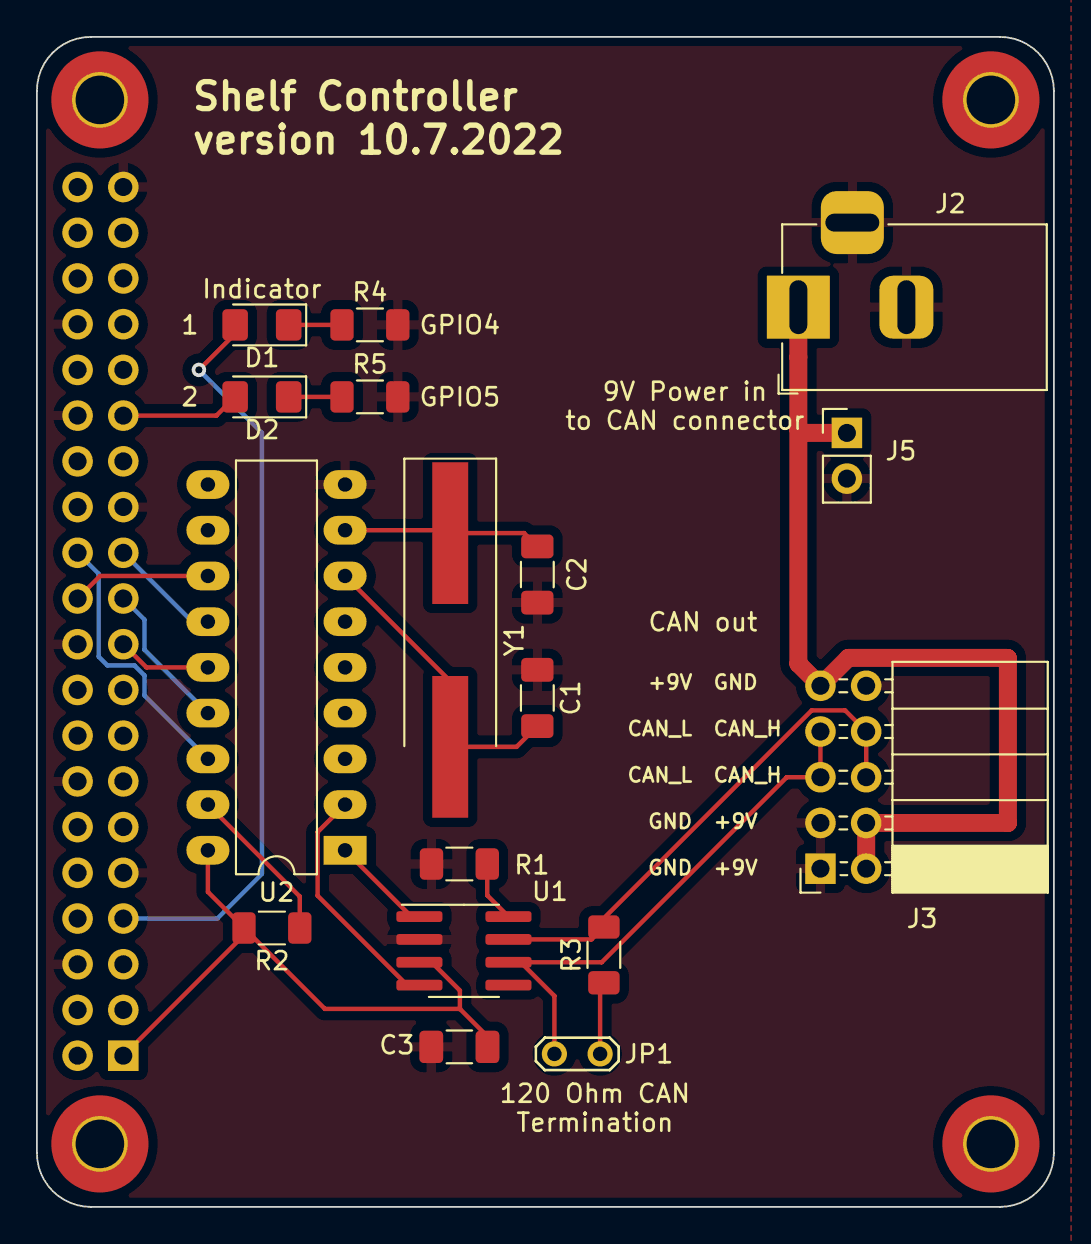
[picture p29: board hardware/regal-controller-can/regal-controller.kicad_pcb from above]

Board: 2 copper layers, 56.5 x 65.0 mm, 22 parts (1 on the bottom side), 21 nets.

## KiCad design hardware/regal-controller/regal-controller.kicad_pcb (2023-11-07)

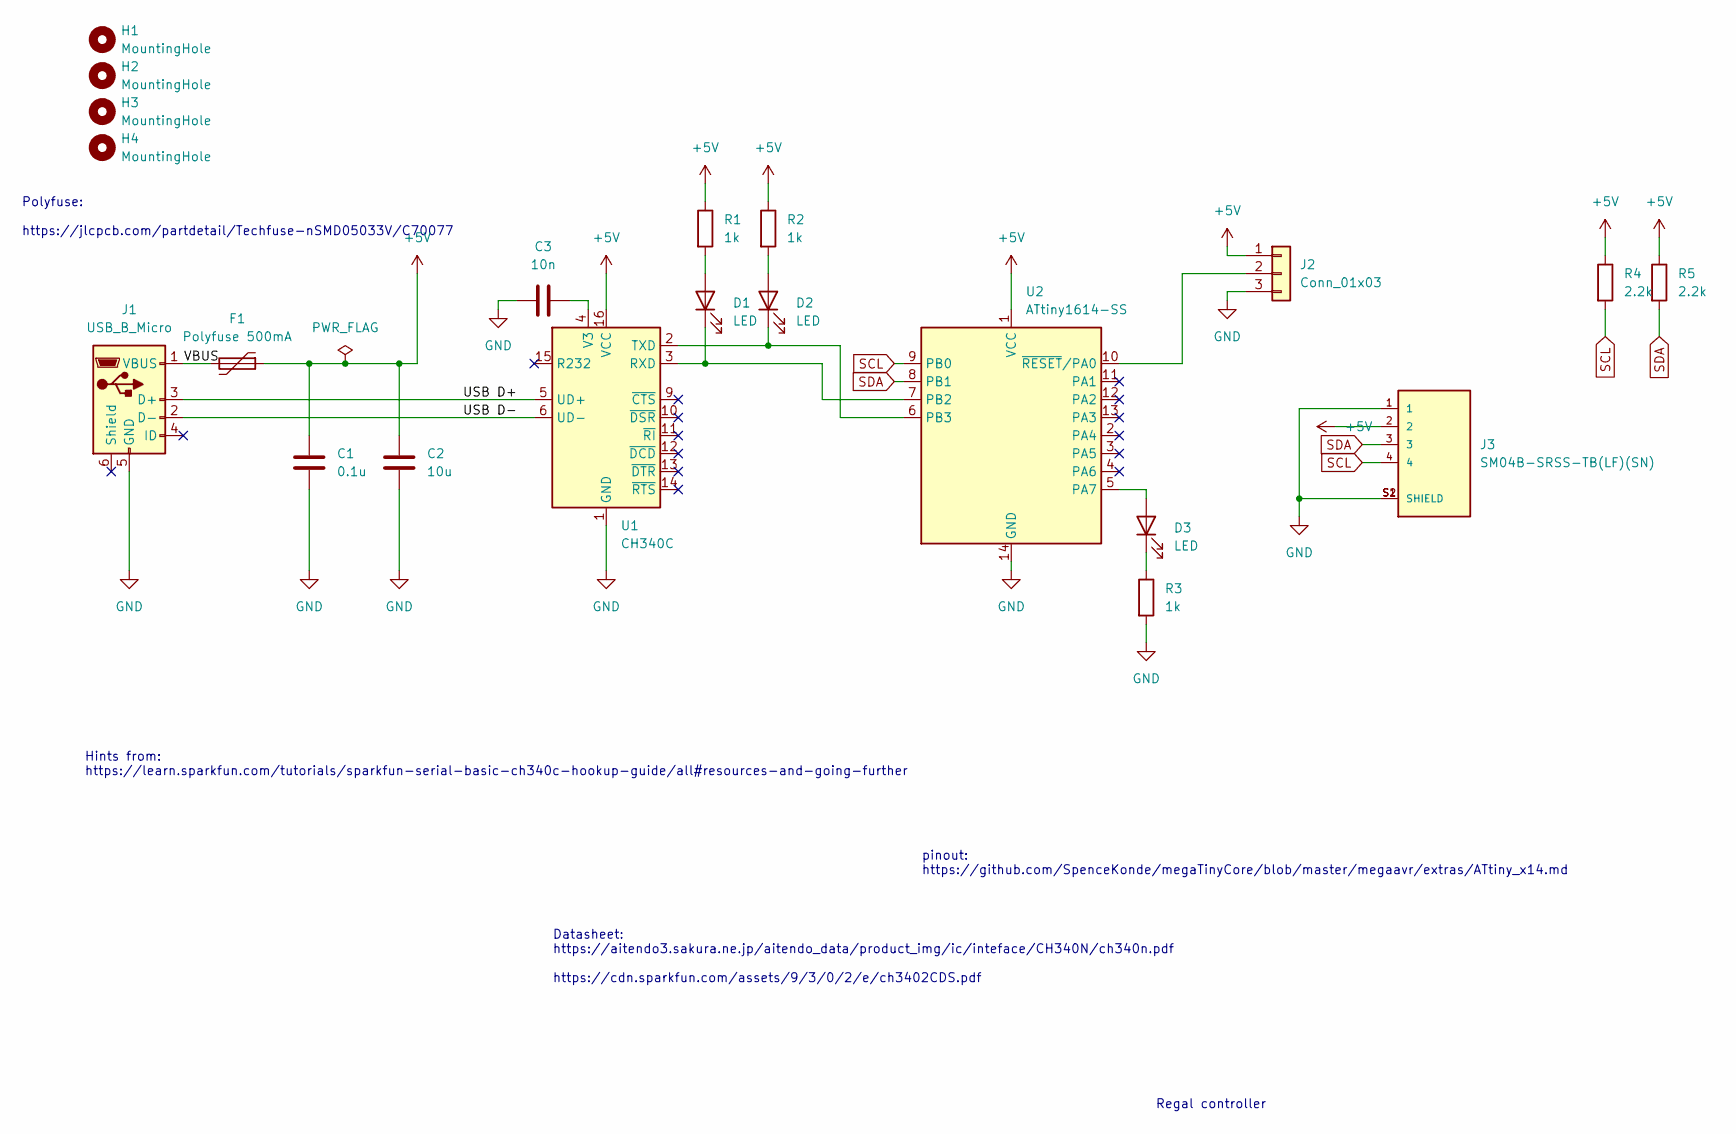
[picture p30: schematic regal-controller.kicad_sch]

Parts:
C1: 0.1u; C_1206_3216Metric
C2: 10u; C_1206_3216Metric
C3: 10n; C_1206_3216Metric
D1, D2, D3: LED; LED_1206_3216Metric
F1: Polyfuse 500mA; Fuse_1206_3216Metric
H1, H2, H3, H4: MountingHole; MountingHole_3.2mm_M3
J1: USB_B_Micro; USB_Micro-B_XKB_U254-051T-4BH83-F1S
J2: Conn_01x03; PinSocket_1x03_P2.54mm_Vertical
J3: SM04B-SRSS-TB(LF)(SN); JST_SM04B-SRSS-TB(LF)(SN)
R1, R2, R3: 1k; R_1206_3216Metric
R4, R5: 2.2k; R_1206_3216Metric
U1: CH340C; SOIC-16_3.9x9.9mm_P1.27mm
U2: ATtiny1614-SS; SOIC-14_3.9x8.7mm_P1.27mm

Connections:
+5V: C1.1, C2.1, F1.1, J2.1, J3.2, R1.1, R2.1, R4.1, R5.1, U1.16 (VCC), U2.1 (VCC)
/USB D+: J1.3 (D+), U1.5 (UD+)
/USB D-: J1.2 (D-), U1.6 (UD-)
/VBUS: F1.2, J1.1 (VBUS)
GND: C1.2, C2.2, C3.1, J1.5 (GND), J2.3, J3.1, J3.S1 (SHIELD), J3.S2 (SHIELD), R3.2, U1.1 (GND), U2.14 (GND)
unnamed: D1.2 (A), R1.2
unnamed: D1.1 (K), U1.3 (RXD), U2.7 (PB2)
unnamed: D2.2 (A), R2.2
unnamed: D2.1 (K), U1.2 (TXD), U2.6 (PB3)
unnamed: D3.2 (A), U2.5 (PA7)
unnamed: D3.1 (K), R3.1
unnamed: J2.2, U2.10 (~RESET/PA0)
unnamed: C3.2, U1.4 (V3)
SCL: J3.4, R4.2, U2.9 (PB0)
SDA: J3.3, R5.2, U2.8 (PB1)

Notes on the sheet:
Regal controller
pinout: https://github.com/SpenceKonde/megaTinyCore/blob/master/megaavr/extras/ATtiny_x14.md
Polyfuse: https://jlcpcb.com/partdetail/Techfuse-nSMD05033V/C70077
Datasheet: https://aitendo3.sakura.ne.jp/aitendo_data/product_img/ic/inteface/CH340N/ch340n.pdf https://cdn.sparkfun.com/assets/9/3/0/2/e/ch3402CDS.pdf
Hints from: https://learn.sparkfun.com/tutorials/sparkfun-serial-basic-ch340c-hookup-guide/all#resources-and-going-further

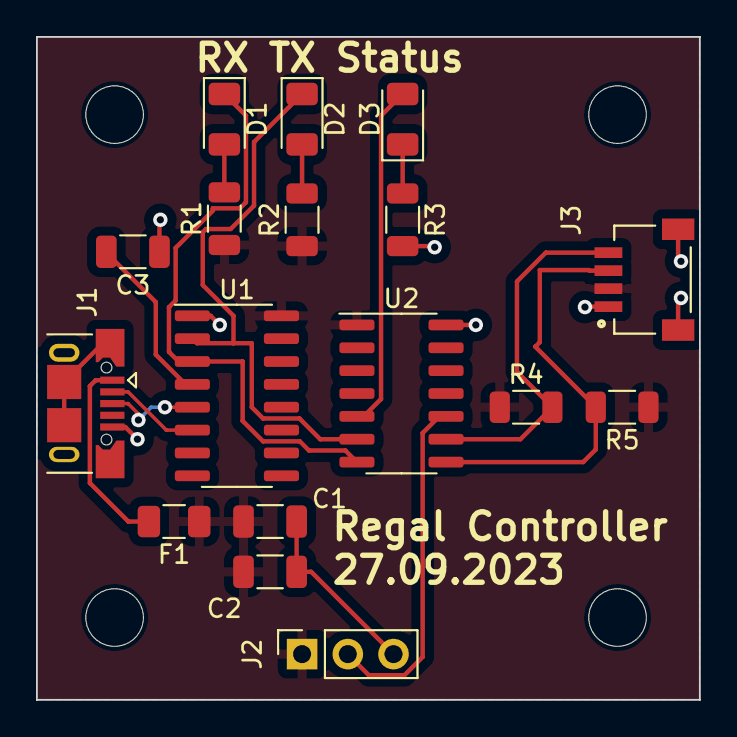
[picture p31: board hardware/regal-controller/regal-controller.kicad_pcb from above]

Board: 2 copper layers, 36.8 x 36.8 mm, 21 parts (0 on the bottom side), 15 nets.

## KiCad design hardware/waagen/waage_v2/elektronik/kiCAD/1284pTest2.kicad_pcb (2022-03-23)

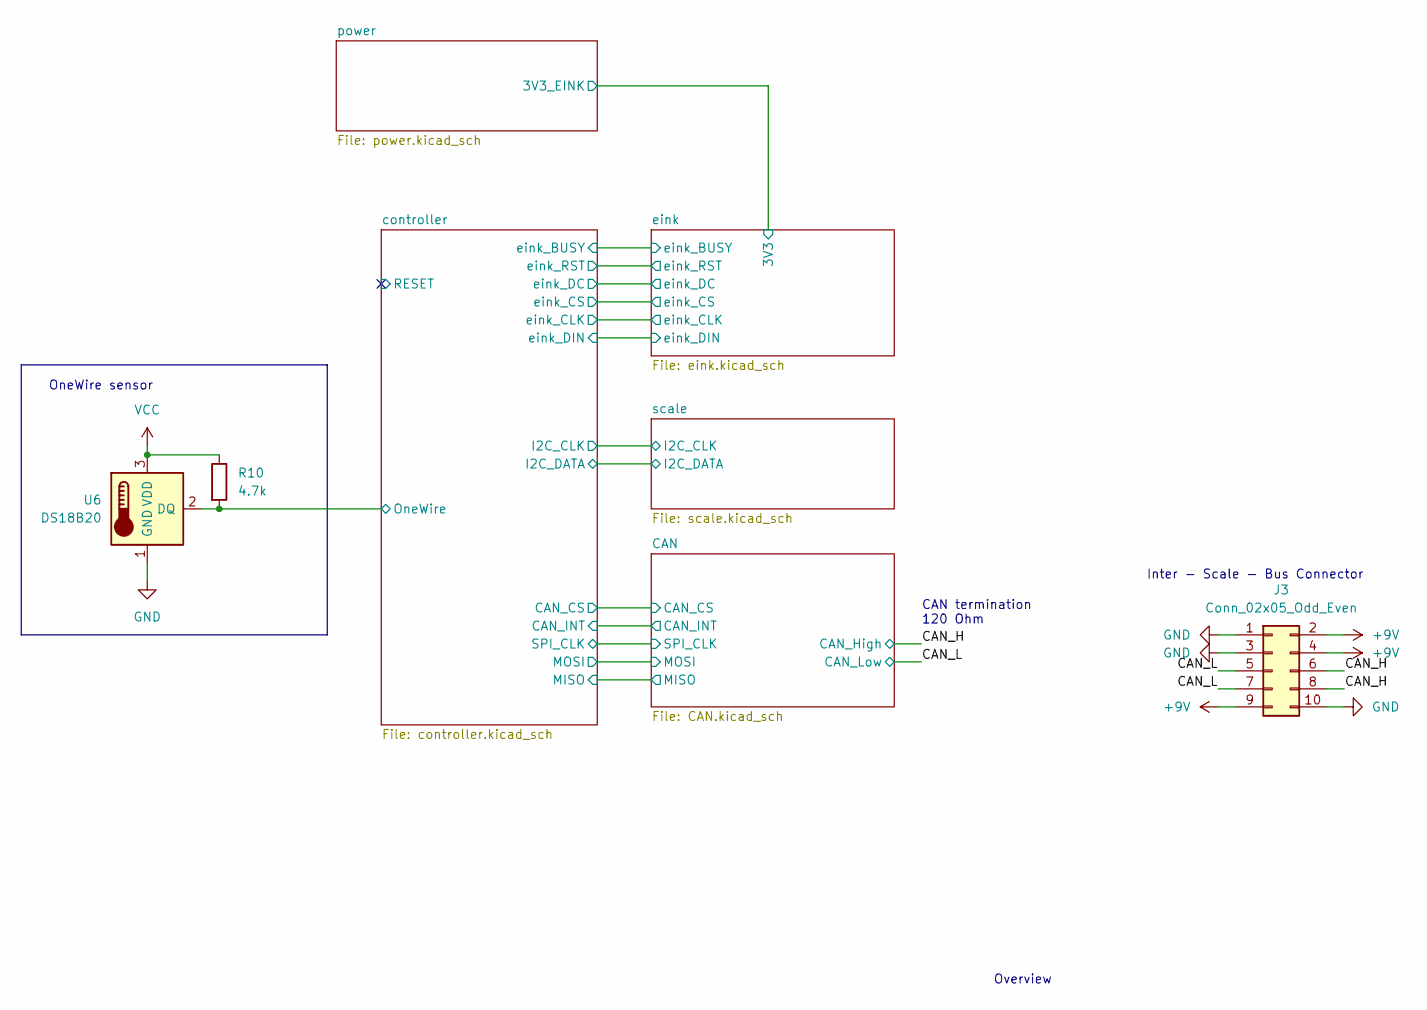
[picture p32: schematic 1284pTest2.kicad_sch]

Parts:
J3: Conn_02x05_Odd_Even; PinSocket_2x05_P2.54mm_Horizontal
R10: 4.7k; R_1206_3216Metric_Pad1.30x1.75mm_HandSolder
U6: DS18B20; TO-92

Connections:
+9V: J3.2, J3.4, J3.9; also elsewhere on the board
/CAN_H: J3.6, J3.8; also elsewhere on the board
/CAN_L: J3.5, J3.7; also elsewhere on the board
/controller/OneWire: R10.2, U6.2 (DQ); also elsewhere on the board
GND: J3.1, J3.3, J3.10, U6.1 (GND); also elsewhere on the board
VCC: R10.1, U6.3 (VDD); also elsewhere on the board

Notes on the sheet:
CAN termination 120 Ohm
Inter - Scale - Bus Connector
Overview
OneWire sensor

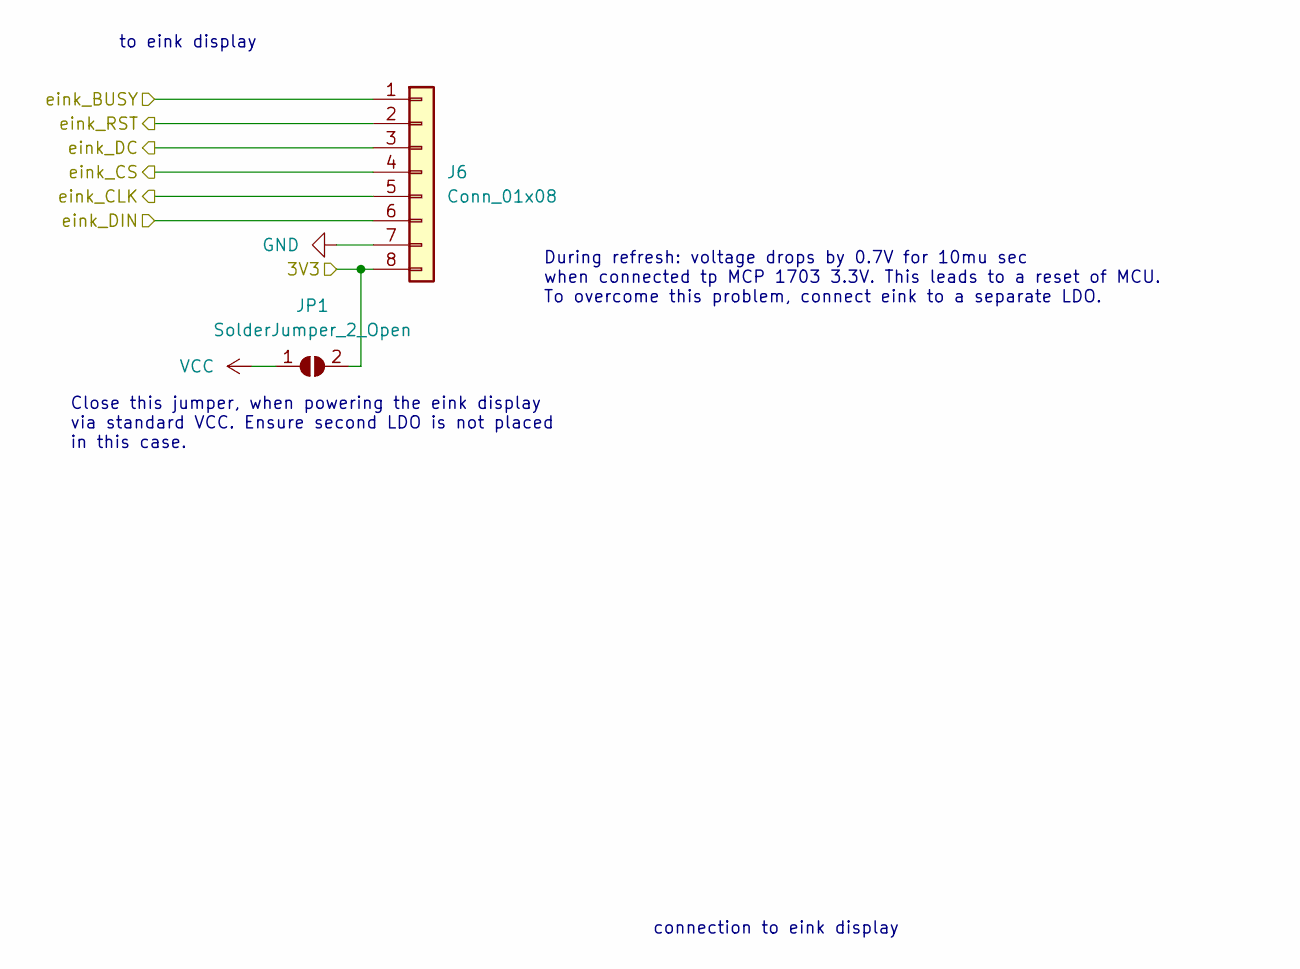
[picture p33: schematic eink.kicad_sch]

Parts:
J6: Conn_01x08; PinHeader_1x08_P2.54mm_Horizontal
JP1: SolderJumper_2_Open; SolderJumper-2_P1.3mm_Open_RoundedPad1.0x1.5mm

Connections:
/controller/eink_BUSY: J6.1; also elsewhere on the board
/controller/eink_CLK: J6.5; also elsewhere on the board
/controller/eink_CS: J6.4; also elsewhere on the board
/controller/eink_DC: J6.3; also elsewhere on the board
/controller/eink_DIN: J6.6; also elsewhere on the board
/controller/eink_RST: J6.2; also elsewhere on the board
/power/3V3_EINK: J6.8, JP1.2 (B); also elsewhere on the board
GND: J6.7; also elsewhere on the board
VCC: JP1.1 (A); also elsewhere on the board

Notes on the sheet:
to eink display
Close this jumper, when powering the eink display via standard VCC. Ensure second LDO is not placed in this case.
During refresh: voltage drops by 0.7V for 10mu sec when connected tp MCP 1703 3.3V. This leads to a reset of MCU. To overcome this problem, connect eink to a separate LDO.
connection to eink display

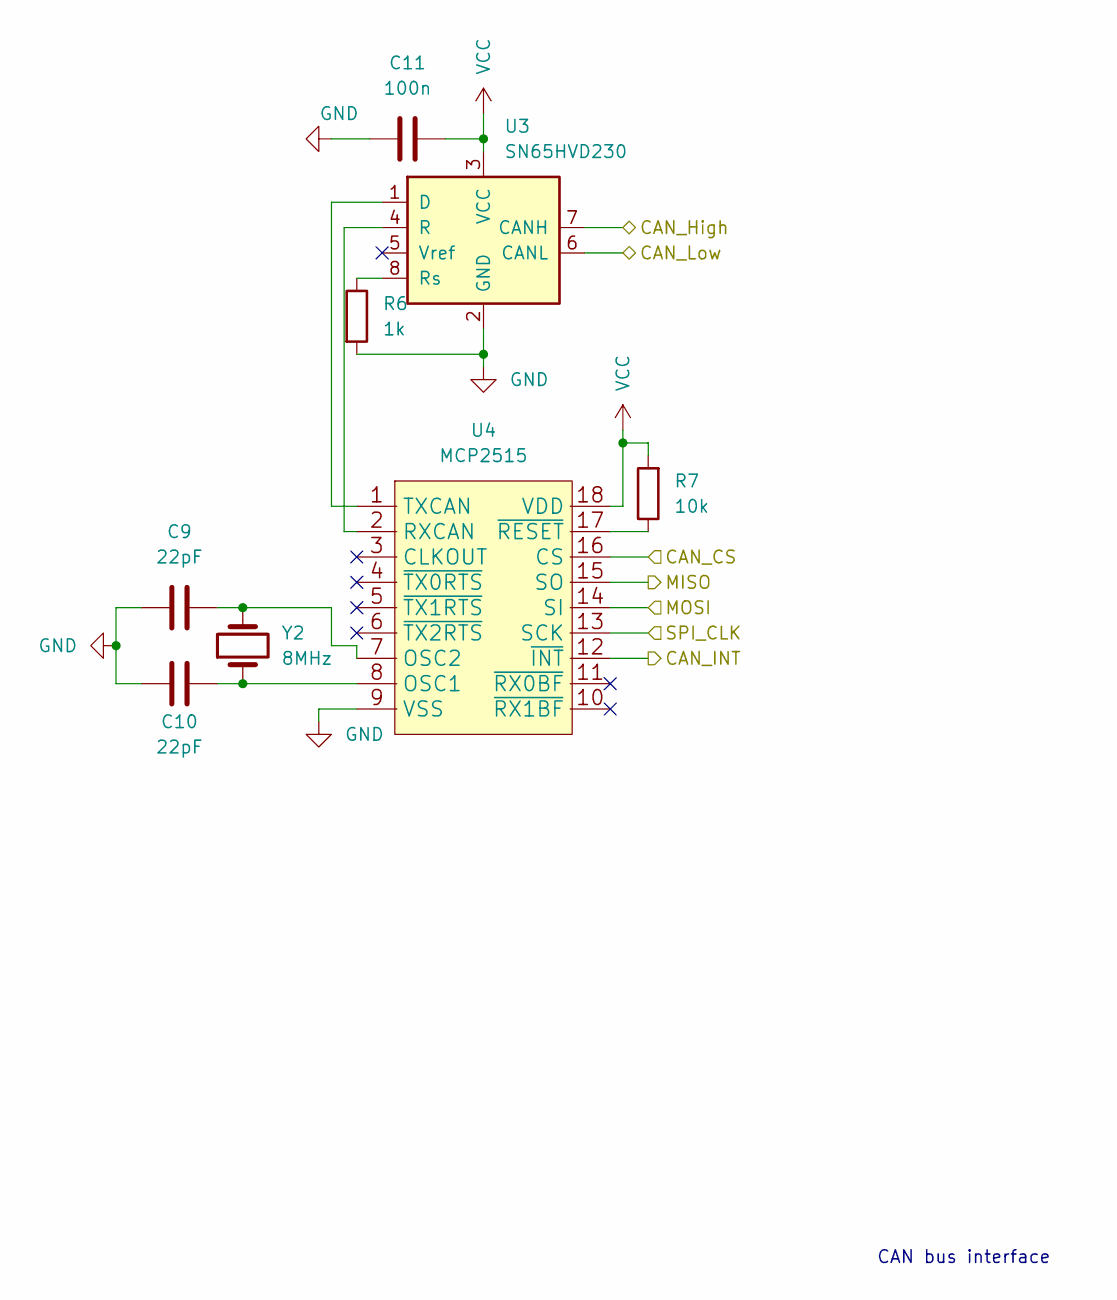
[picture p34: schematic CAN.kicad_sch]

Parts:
C9, C10: 22pF; C_1206_3216Metric_Pad1.33x1.80mm_HandSolder
C11: 100n; C_1206_3216Metric_Pad1.33x1.80mm_HandSolder
R6: 1k; R_1206_3216Metric_Pad1.30x1.75mm_HandSolder
R7: 10k; R_1206_3216Metric_Pad1.30x1.75mm_HandSolder
U3: SN65HVD230; SOIC-8_3.9x4.9mm_P1.27mm
U4: MCP2515; DIP-18_W7.62mm_LongPads
Y2: 8MHz; Crystal_SMD_HC49-SD_HandSoldering

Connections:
/CAN/CAN_CS: U4.16 (CS); also elsewhere on the board
/CAN/CAN_INT: U4.12 (~INT); also elsewhere on the board
/CAN/MISO: U4.15 (SO); also elsewhere on the board
/CAN/MOSI: U4.14 (SI); also elsewhere on the board
/CAN/SPI_CLK: U4.13 (SCK); also elsewhere on the board
/CAN_H: U3.7 (CANH); also elsewhere on the board
/CAN_L: U3.6 (CANL); also elsewhere on the board
GND: C9.1, C10.1, C11.1, R6.2, U3.2 (GND), U4.9 (VSS); also elsewhere on the board
unnamed: C9.2, U4.7 (OSC2), Y2.2
unnamed: C10.2, U4.8 (OSC1), Y2.1
unnamed: R6.1, U3.8 (Rs)
unnamed: R7.1, U4.17 (~RESET)
unnamed: U3.1 (D), U4.1 (TXCAN)
unnamed: U3.4 (R), U4.2 (RXCAN)
VCC: C11.2, R7.2, U3.3 (VCC), U4.18 (VDD); also elsewhere on the board

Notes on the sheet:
CAN bus interface

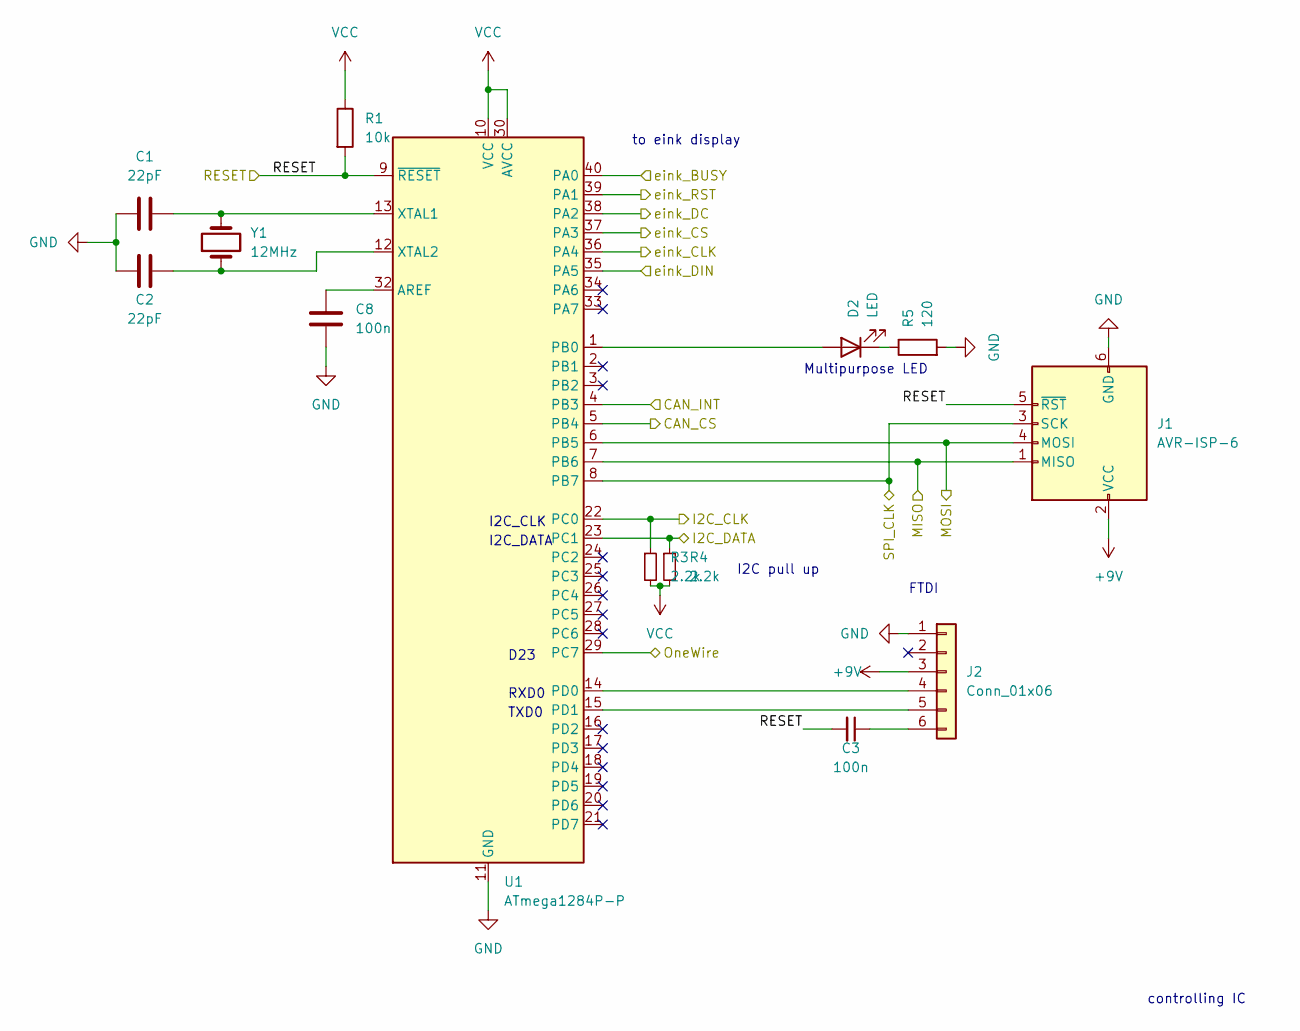
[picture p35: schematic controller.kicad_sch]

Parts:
C1, C2: 22pF; C_1206_3216Metric_Pad1.33x1.80mm_HandSolder
C3, C8: 100n; C_1206_3216Metric_Pad1.33x1.80mm_HandSolder
D2: LED; LED_1206_3216Metric_Pad1.42x1.75mm_HandSolder
J1: AVR-ISP-6; PinHeader_2x03_P2.54mm_Vertical
J2: Conn_01x06; PinSocket_1x06_P2.54mm_Vertical
R1: 10k; R_1206_3216Metric_Pad1.30x1.75mm_HandSolder
R3, R4: 2.2k; R_1206_3216Metric_Pad1.30x1.75mm_HandSolder
R5: 120; R_1206_3216Metric_Pad1.30x1.75mm_HandSolder
U1: ATmega1284P-P; DIP-40_W15.24mm
Y1: 12MHz; Crystal_SMD_HC49-SD_HandSoldering

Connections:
+9V: J1.2 (VCC), J2.3; also elsewhere on the board
/CAN/CAN_CS: U1.5 (PB4); also elsewhere on the board
/CAN/CAN_INT: U1.4 (PB3); also elsewhere on the board
/CAN/MISO: J1.1 (MISO), U1.7 (PB6); also elsewhere on the board
/CAN/MOSI: J1.4 (MOSI), U1.6 (PB5); also elsewhere on the board
/CAN/SPI_CLK: J1.3 (SCK), U1.8 (PB7); also elsewhere on the board
/controller/I2C_CLK: R3.1, U1.22 (PC0); also elsewhere on the board
/controller/I2C_DATA: R4.1, U1.23 (PC1); also elsewhere on the board
/controller/OneWire: U1.29 (PC7); also elsewhere on the board
/controller/RESET: C3.2, J1.5 (~RST), R1.2, U1.9 (~RESET)
/controller/eink_BUSY: U1.40 (PA0); also elsewhere on the board
/controller/eink_CLK: U1.36 (PA4); also elsewhere on the board
/controller/eink_CS: U1.37 (PA3); also elsewhere on the board
/controller/eink_DC: U1.38 (PA2); also elsewhere on the board
/controller/eink_DIN: U1.35 (PA5); also elsewhere on the board
/controller/eink_RST: U1.39 (PA1); also elsewhere on the board
GND: C1.1, C2.1, C8.2, J1.6 (GND), J2.1, R5.2, U1.11 (GND), U1.31 (GND); also elsewhere on the board
unnamed: C1.2, U1.13 (XTAL1), Y1.2
unnamed: C2.2, U1.12 (XTAL2), Y1.1
unnamed: C3.1, J2.6
unnamed: C8.1, U1.32 (AREF)
unnamed: D2.1 (K), R5.1
unnamed: D2.2 (A), U1.1 (PB0)
unnamed: J2.4, U1.14 (PD0)
unnamed: J2.5, U1.15 (PD1)
VCC: R1.1, R3.2, R4.2, U1.10 (VCC), U1.30 (AVCC); also elsewhere on the board

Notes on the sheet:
I2C pull up
Multipurpose LED
I2C_DATA
to eink display
FTDI
TXD0
D23
controlling IC
RXD0
I2C_CLK

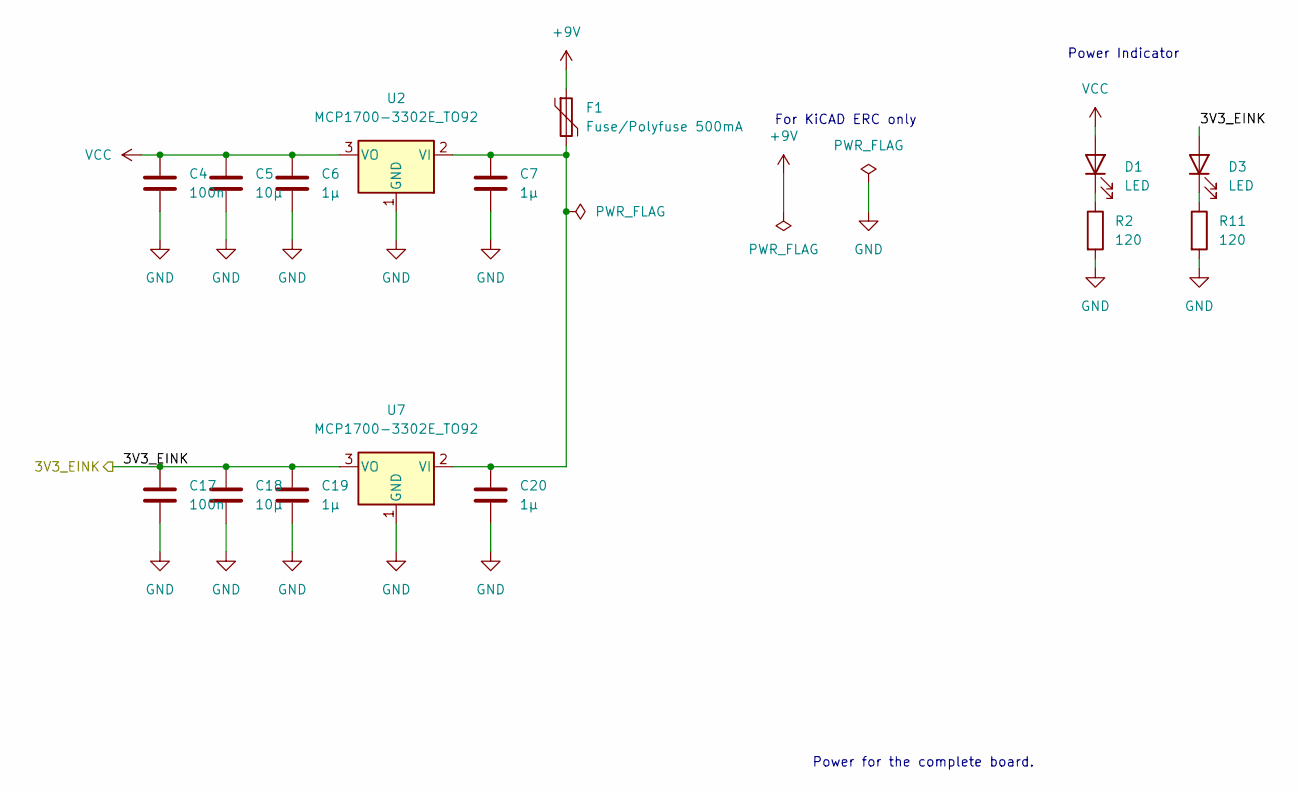
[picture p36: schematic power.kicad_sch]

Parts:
C4, C17: 100n; C_1206_3216Metric_Pad1.33x1.80mm_HandSolder
C5, C18: 10µ; C_1206_3216Metric_Pad1.33x1.80mm_HandSolder
C6, C7, C19, C20: 1µ; C_1206_3216Metric_Pad1.33x1.80mm_HandSolder
D1, D3: LED; LED_1206_3216Metric_Pad1.42x1.75mm_HandSolder
F1: Fuse/Polyfuse 500mA; Fuse_2512_6332Metric_Pad1.52x3.35mm_HandSolder
R2, R11: 120; R_1206_3216Metric_Pad1.30x1.75mm_HandSolder
U2, U7: MCP1700-3302E_TO92; TO-92_Inline

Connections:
+9V: F1.1; also elsewhere on the board
/power/3V3_EINK: C17.1, C18.1, C19.1, D3.2 (A), U7.3 (VO); also elsewhere on the board
GND: C4.2, C5.2, C6.2, C7.2, C17.2, C18.2, C19.2, C20.2, R2.2, R11.2, U2.1 (GND), U7.1 (GND); also elsewhere on the board
unnamed: C7.1, C20.1, F1.2, U2.2 (VI), U7.2 (VI)
unnamed: D1.1 (K), R2.1
unnamed: D3.1 (K), R11.1
VCC: C4.1, C5.1, C6.1, D1.2 (A), U2.3 (VO); also elsewhere on the board

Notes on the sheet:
For KiCAD ERC only
Power Indicator
Power for the complete board.

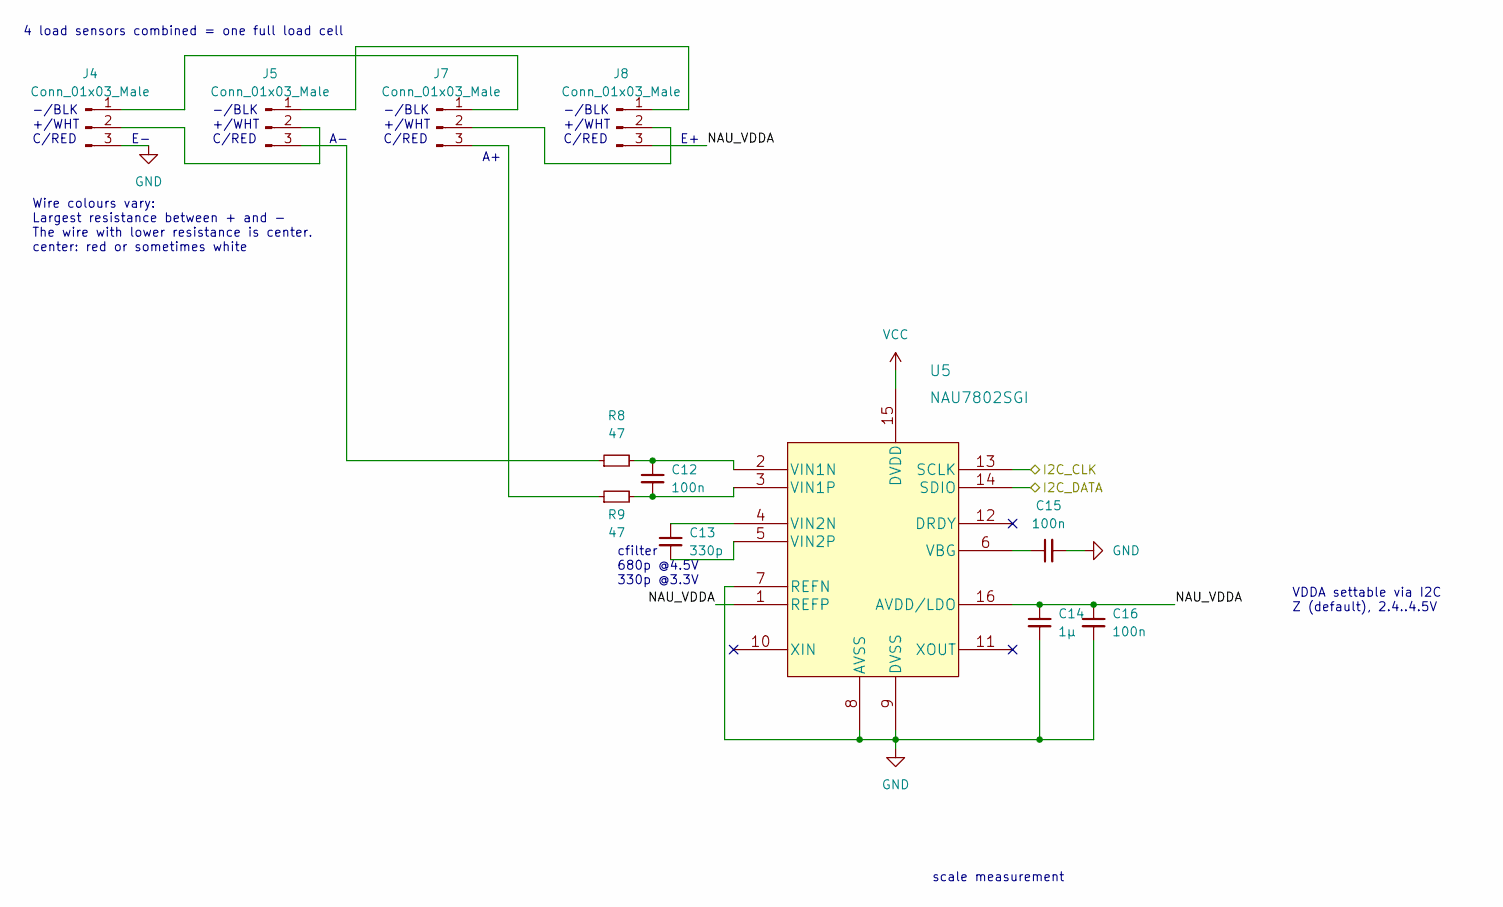
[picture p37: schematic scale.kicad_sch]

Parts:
C12, C15, C16: 100n; C_1206_3216Metric_Pad1.33x1.80mm_HandSolder
C13: 330p; C_1206_3216Metric_Pad1.33x1.80mm_HandSolder
C14: 1µ; C_1206_3216Metric_Pad1.33x1.80mm_HandSolder
J4, J5, J7, J8: Conn_01x03_Male; SolderWire-0.1sqmm_1x03_P3.6mm_D0.4mm_OD1mm_Relief2x
R8, R9: 47; R_1206_3216Metric_Pad1.30x1.75mm_HandSolder
U5: NAU7802SGI

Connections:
/controller/I2C_CLK: U5.13 (SCLK); also elsewhere on the board
/controller/I2C_DATA: U5.14 (SDIO); also elsewhere on the board
/scale/NAU_VDDA: C14.1, C16.1, J8.3, U5.1 (REFP), U5.16 (AVDD/LDO)
GND: C14.2, C15.2, C16.2, J4.3, U5.7 (REFN), U5.8 (AVSS), U5.9 (DVSS); also elsewhere on the board
unnamed: C12.1, R8.2, U5.2 (VIN1N)
unnamed: C12.2, R9.2, U5.3 (VIN1P)
unnamed: C13.1, U5.4 (VIN2N)
unnamed: C13.2, U5.5 (VIN2P)
unnamed: C15.1, U5.6 (VBG)
unnamed: J4.1, J7.1
unnamed: J4.2, J5.2
unnamed: J5.1, J8.1
unnamed: J5.3, R8.1
unnamed: J7.2, J8.2
unnamed: J7.3, R9.1
VCC: U5.15 (DVDD); also elsewhere on the board

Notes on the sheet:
-/BLK +/WHT C/RED
cfilter 680p @4.5V 330p @3.3V
VDDA settable via I2C Z (default), 2.4..4.5V
Wire colours vary: Largest resistance between + and - The wire with lower resistance is center. center: red or sometimes white
scale measurement
4 load sensors combined = one full load cell

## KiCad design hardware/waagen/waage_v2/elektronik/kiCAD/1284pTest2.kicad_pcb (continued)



Board: 2 copper layers, 49.8 x 126.8 mm, 53 parts (46 on the bottom side), 50 nets.

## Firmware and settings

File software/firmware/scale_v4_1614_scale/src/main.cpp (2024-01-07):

// Scale

#include <Wire.h>
#include <SoftWire.h>
#include <AsyncDelay.h>
#include <version.h>
#include <EEPROM.h>

// Soft I2C START
SoftWire sw(6, 7);
// These buffers must be at least as large as the largest read or write you perform.
char swTxBuffer[16];
char swRxBuffer[16];

AsyncDelay readInterval;
// Soft I2C END

// NAU Start
// Funktioniert mit Soft I2C nur mit geänderter Library
#include "SparkFun_Qwiic_Scale_NAU7802_Arduino_Library.h" // Click here to get the library: http://librarymanager/All#SparkFun_NAU8702

NAU7802 myScale;                          // Create instance of the NAU7802 class
#define NUMBER_OF_SCALE_READINGS_BUFFER 8 // should multiple of 2^N for fast division
long last_scale_raw_readings[NUMBER_OF_SCALE_READINGS_BUFFER];
byte last_scale_raw_readings_ringbuffer_index = 0; // points to the actual index used
long averaged_reading_sum = 0;                     // helper variable to average all entries in last_scale_raw_readings. needs to be divided by NUMBER_OF_SCALE_READINGS_BUFFER to get real average
long averaged_reading = 0;                         // regularly updated: averaged_reading_sum/NUMBER_OF_SCALE_READINGS_BUFFER
long last_scale_raw_reading = 0;                   // raw value from ADC
// NAU END

// Data from EEPROM
byte eeprom_i2c_address;
// Data from serial number chip
byte device_mac_address[6];

bool answer_bit = false; // If set to false, device will not answer on I2C address 0x8
bool update_i2c_address_from_eeprom = false;
bool restart_at_next_possibility = false;
byte register_select_readout = 0;
byte register_compare_mac_address[6];
byte register_eeprom_address_to_read = 0;

/// Watchdog, see: https://github.com/SpenceKonde/megaTinyCore/blob/master/megaavr/extras/Ref_Reset.md
void wdt_enable()
{
  _PROTECTED_WRITE(WDT.CTRLA, WDT_PERIOD_4KCLK_gc); // no window, 4 seconds
}

void wdt_reset()
{
  __asm__ __volatile__("wdr" ::);
}

void wdt_disable()
{
  _PROTECTED_WRITE(WDT.CTRLA, 0);
}
/// Watchdog end

/// Reset Device via Software
// Better do not use during I2C access: No ack to I2C will be send!
// Better let the watchdog bite
void resetViaSWR()
{
  _PROTECTED_WRITE(RSTCTRL.SWRR, 1);
}
/// END Reset

//*********** CHIP Self Test Routines Start ****************
// Chip self test
// Hints from here: https://forum.arduino.cc/t/reading-the-system-voltage-on-the-new-attiny-1-series/644885/7
#define chip_test_RESULTCOUNT 4
int16_t chip_test_results[chip_test_RESULTCOUNT];
int32_t chip_test_sum;
int16_t chip_test_average;
#define chip_test_results_i2c_buffer_LENGTH 11
int16_t chip_test_results_i2c_buffer[chip_test_results_i2c_buffer_LENGTH];

void chip_test_showHex(unsigned char b)
{
  if (b <= 0xf)
    Serial.print("0");
  Serial.print(b, HEX);
}

void chip_test_printRegisters()
{
  Serial.print("ADC0.MUXPOS: ");
  chip_test_showHex(ADC0.MUXPOS);
  Serial.print("  ADC0.CTRLC: ");
  chip_test_showHex(ADC0.CTRLC);
  Serial.print("  VREF.CTRLA: ");
  chip_test_showHex(VREF.CTRLA);
  Serial.println();
}

int16_t chip_test_runTest_without_expected(uint8_t reference, uint8_t pin)
{
  // clearResults
  for (byte x = 0; x < chip_test_RESULTCOUNT; x++)
  {
    chip_test_results[x] = -1;
  }
  chip_test_sum = 0;
  chip_test_average = 0;

  // Start test
  Serial.print("Now testing pin 0x");
  chip_test_showHex(pin);
  Serial.println();
  analogReference(reference);
  for (byte x = 0; x < chip_test_RESULTCOUNT; x++)
  {
    chip_test_results[x] = analogRead(pin);
  }
  chip_test_printRegisters();
  for (byte x = 0; x < chip_test_RESULTCOUNT; x++)
  {
    chip_test_sum += chip_test_results[x];
  }
  Serial.print("Average: ");
  chip_test_average = chip_test_sum / chip_test_RESULTCOUNT;
  Serial.println(chip_test_average);
  return chip_test_average;
}

int8_t chip_test_runTest(uint8_t reference, uint8_t pin, int16_t expected)
{
  chip_test_runTest_without_expected(reference, pin);
  Serial.print("Expected: ");
  Serial.println(expected);
  int16_t diff = expected - chip_test_average;
  if (diff < 0)
  {
    diff -= 2 * diff;
  }
  if (diff < 8)
  {
    Serial.println("PASS\n");
    // return 0;
  }
  return chip_test_average;
}

void chip_test_prepare()
{
  Serial.println("testAnalogReference");
  analogWrite(PIN_A6, 127); // Output 50% of max voltage from DAC, DAC VREF = 0.55 V, so this is 0.275 V
  Serial.println("Initial state of ADC registers: ");
  chip_test_printRegisters();
}

void chip_test_perform()
{
  Serial.println("START START START START START START START START START START");
  Serial.println("Start Test with VREF=0.55V");
  chip_test_results_i2c_buffer[0] = 508; // chip_test_runTest(INTERNAL0V55,ADC_DAC0, 508);

  Serial.println("Start Test with VREF= 1.1V");
  chip_test_results_i2c_buffer[1] = chip_test_runTest(INTERNAL1V1, ADC_DAC0, 254);

  Serial.println("Start Test with VREF= 1.5V");
  chip_test_results_i2c_buffer[2] = chip_test_runTest(INTERNAL1V5, ADC_DAC0, 186);

  Serial.println("Start Test with VREF= 2.5VV");
  chip_test_results_i2c_buffer[3] = chip_test_runTest(INTERNAL2V5, ADC_DAC0, 112);

  Serial.println("Start Test with VREF= 4.34V");
  chip_test_results_i2c_buffer[4] = chip_test_runTest(INTERNAL4V34, ADC_DAC0, 64);

  Serial.println("Start Test with VREF= Vcc 5.0V");
  int16_t vscale = chip_test_runTest_without_expected(VDD, ADC_DAC0);
  chip_test_results_i2c_buffer[5] = vscale;
  Serial.print("Voltage is: ");
  Serial.print(chip_test_average * 89);
  Serial.println("mV\n");

  Serial.println("Start Test with VREF= Vcc (5.0V) Internal Ref 0.55V");
  VREF.CTRLA = VREF_ADC0REFSEL_0V55_gc;
  chip_test_results_i2c_buffer[6] = chip_test_runTest(VDD, ADC_INTREF, (113L * vscale) / 56);

  Serial.println("Start Test with VREF= Vcc (5.0V) Internal Ref 1.1V");
  VREF.CTRLA = VREF_ADC0REFSEL_1V1_gc;
  chip_test_results_i2c_buffer[7] = chip_test_runTest(VDD, ADC_INTREF, (225L * vscale) / 56);

  Serial.println("Start Test with VREF= Vcc (5.0V) Internal Ref 1.5V");
  VREF.CTRLA = VREF_ADC0REFSEL_1V5_gc;
  chip_test_results_i2c_buffer[8] = chip_test_runTest(VDD, ADC_INTREF, (307L * vscale) / 56);

  Serial.println("Start Test with VREF= Vcc (5.0V) Internal Ref 2.5V");
  VREF.CTRLA = VREF_ADC0REFSEL_2V5_gc;
  chip_test_results_i2c_buffer[9] = chip_test_runTest(VDD, ADC_INTREF, (512L * vscale) / 56);

  Serial.println("Start Test with VREF= Vcc (5.0V) Internal Ref 4.34V");
  VREF.CTRLA = VREF_ADC0REFSEL_4V34_gc;
  chip_test_results_i2c_buffer[10] = chip_test_runTest(VDD, ADC_INTREF, (888L * vscale) / 56);
}
//*********** CHIP Self Test End *****

// Write request handler, expected: Wire.read
void receiveEvent(int numBytes)
{
  uint8_t addr = Wire.getIncomingAddress(); // get the address that triggered this function
  addr = addr >> 1;                         // shift to the address bits, not r/w bit.

  Serial.print("Write by master on address: 0x");
  Serial.print(addr, HEX);
  Serial.print(" length: ");
  Serial.println(numBytes);

  if (addr == 0x0)
  { // General call address
    // while (Wire.available())
    if (numBytes >= 1)
    {
      char c = Wire.read();
      Serial.print("data: 0x");
      Serial.println(c, HEX);
      Serial.flush();

      if (c == 0x00)
      { // Reset scale
        Serial.println("Restart scale");
        Serial.flush();
        delay(100); // To allow serial data flush
        restart_at_next_possibility = true;
      }
      if (c == 0x01)
      { // Reset answer bit
        answer_bit = true;
      }
      if ((c == 0x02) && (numBytes == 8))
      { // Set I2C address, 8 bytes: 0x2 6bytes MAC address and 1byte I2C address
        byte temp_mac_address[6];
        for (byte i = 0; i < 6; i++)
        {
          temp_mac_address[i] = Wire.read();
        }
        byte temp_i2c_address = Wire.read();

        // check
        bool equal = true;
        for (byte i = 0; i < 6; i++)
        {
          if (device_mac_address[i] != temp_mac_address[i])
          {
            equal = false;
          }
        }

        // Set I2C address
        if (equal)
        {
          answer_bit = false;
          EEPROM.write(0, temp_i2c_address);
          Serial.print("New I2C address set to: ");
          Serial.print(temp_i2c_address);
          Serial.println(". Restarting...");
          Serial.flush();
          update_i2c_address_from_eeprom = true; // set flag to update later in loop, to complete actual I2C request
        }
      }
      if ((c == 3) && (numBytes == 7)) // set reference MAC address
      {
        for (byte i = 0; i < 6; i++)
        {
          register_compare_mac_address[i] = Wire.read();
        }
      }
      if (c == 0x04)
      {
        digitalWrite(LED_BUILTIN, LOW); // Switch off
      }
      if (c == 0x05)
      {
        digitalWrite(LED_BUILTIN, HIGH); // Switch on
      }
    }
  }

  if (addr == eeprom_i2c_address)
  {
    byte c = Wire.read();

    if (c == 0x00)
    { // nächtes Lesen enthält Waagen-Wert
      register_select_readout = 0;
      Serial.println("register_select_readout set to 0.");
    }
    if (c == 0x01)
    { // nächtes Lesen enthält MAC-Adresse und LED-Status
      register_select_readout = 1;
      Serial.println("register_select_readout set to 1.");
    }
    if (c == 0x02)
    {                                 // LED aus
      digitalWrite(LED_BUILTIN, LOW); // Switch off
    }
    if (c == 0x03)
    {                                  // LED on
      digitalWrite(LED_BUILTIN, HIGH); // Switch on
    }
    if (c == 0x04)
    { // nächtes Lesen enthält Ergebnis des Selst Tests
      register_select_readout = 2;
      Serial.println("register_select_readout set to 2.");
      chip_test_prepare();
    }
    //Write to EEPROM
    //3 bytes expected:
    //1st = 0x05
    //2nd = address
    //3rd = data byte
    if ( (c == 0x05) && (numBytes == 3) )
    {  //write to EEPROM
      byte a = Wire.read();
      byte v = Wire.read();
      Serial.print("Write to EEPROM. address: ");
      Serial.print(a);
      Serial.print(" and value ");
      Serial.println(v);
      EEPROM.write(a, v);
    }
    //Prepare Read from EEPROM
    //2 bytes expected:
    //1st = 0x05
    //2nd = address
    //After this command, read from i2c device to get data
    if ( (c == 0x06) && (numBytes == 2) )
    { 
      register_select_readout = 3;
      register_eeprom_address_to_read = Wire.read();
    }
  }
}

// Read request handler, expected: Wire.write
void requestHandler()
{
  uint8_t bytes_read = Wire.getBytesRead();
  uint8_t addr = Wire.getIncomingAddress(); // get the address that triggered this function
  addr = addr >> 1;                         // shift to the address bits, not r/w bit.

  Serial.print("Read by master on address: 0x");
  Serial.println(addr, HEX);

  if ((addr == 8) && (answer_bit))
  {
    bool result_e_l_c = true; // true if device_mac_address <= register_compare_mac_address
    for (byte i = 0; i < 6; i++)
    {
      Serial.print("Compare: ");
      Serial.print((uint8_t)device_mac_address[i], HEX);
      Serial.print(" with ");
      Serial.println((uint8_t)register_compare_mac_address[i], HEX);
      if (device_mac_address[i] > register_compare_mac_address[i])
      {
        result_e_l_c = false;
        break; // skip for loop
      }
      if (device_mac_address[i] < register_compare_mac_address[i])
      {
        result_e_l_c = true;
        break; // skip for loop
      }
    }

    if (result_e_l_c)
    {
      Wire.write(0x00); // dominant on I2C bus
    }
    else
    {
      Wire.write(0xFF);
    }
  }

  if (addr == eeprom_i2c_address)
  {
    if (register_select_readout == 0)
    { // 4 Bytes, Waagenwerte
      Wire.write((byte *)&averaged_reading, sizeof(averaged_reading));
    }

    if (register_select_readout == 1)
    { // 7 Bytes, MAC Adresse und LED-Status und 4 bytes BUILD_NUMBER und 2 bytes HARDWARE_REVISION
      for (byte i = 0; i < 6; i++)
      {
        Wire.write(device_mac_address[i]);
      }
      Wire.write(digitalRead(LED_BUILTIN));

      Wire.write((byte)((((long int)BUILD_NUMBER)>>24) & 0xff));
      Wire.write((byte)((((long int)BUILD_NUMBER)>>16) & 0xff));
      Wire.write((byte)((((long int)BUILD_NUMBER)>>8) & 0xff));
      Wire.write((byte)((((long int)BUILD_NUMBER)>>0) & 0xff));

      Wire.write(0);//Hardware Revision
      Wire.write(1);//Hardware Revision
    }

    if (register_select_readout == 2)
    { // chip_test_results_i2c_buffer_LENGTH *2 Bytes: RESULTS FROM SELF TEST
      for (byte i = 0; i < chip_test_results_i2c_buffer_LENGTH; i++)
      {
        Wire.write((chip_test_results_i2c_buffer[i] >> 8) & 0xFF);
        Wire.write((chip_test_results_i2c_buffer[i]) & 0xFF);
      }
    }

    if (register_select_readout == 3)
    { //1 byte answer
      Wire.write(EEPROM.read(register_eeprom_address_to_read));
    }

  }
}

void setup()
{
  // Sleep at the beginning, to make sure voltages are stabilised,
  // see: https://github.com/SpenceKonde/megaTinyCore/tree/master/megaavr/libraries/EEPROM
  delay(100);

  // Enable Watchdog
  wdt_enable();

  Serial.begin(115200);
  Serial.print("scale version: ");
  Serial.println(VERSION);

  // SIGROW.SERNUM0 .. SERNUM9, eg:
  //  30 54 43 30 39 53 F7 75 13 45
  //  30 54 43 30 39 53 D7 FA 13 46
  //  30 54 43 30 39 53 77 F1 13 38
  //  see: https://microchip.my.site.com/s/article/Serial-number-in-AVR---Mega-Tiny-devices
  Serial.print("ATTiny chip serial: ");
  Serial.print(SIGROW.SERNUM0, HEX); // Lot Number 2nd Char
  Serial.print(" ");
  Serial.print(SIGROW.SERNUM1, HEX); // Lot Number 1st Char
  Serial.print(" ");
  Serial.print(SIGROW.SERNUM2, HEX); // Lot Number 4th Char
  Serial.print(" ");
  Serial.print(SIGROW.SERNUM3, HEX); // Lot Number 3rd Char
  Serial.print(" ");
  Serial.print(SIGROW.SERNUM4, HEX); // Lot Number 6th Char
  Serial.print(" ");
  Serial.print(SIGROW.SERNUM5, HEX); // Lot Number 5th Char
  Serial.print(" ");
  Serial.print(SIGROW.SERNUM6, HEX); // Reserved
  Serial.print(" ");
  Serial.print(SIGROW.SERNUM7, HEX); // Wafer Number
  Serial.print(" ");
  Serial.print(SIGROW.SERNUM8, HEX); // Y-coordinate
  Serial.print(" ");
  Serial.println(SIGROW.SERNUM9, HEX); // X-coordinate

  // Set mac address
  device_mac_address[0] = SIGROW.SERNUM2; // Lot Number 4th Char
  device_mac_address[1] = SIGROW.SERNUM5; // Lot Number 5th Char
  device_mac_address[2] = SIGROW.SERNUM4; // Lot Number 6th Char
  device_mac_address[3] = SIGROW.SERNUM7; // Wafer Number
  device_mac_address[4] = SIGROW.SERNUM8; // Y-coordinate
  device_mac_address[5] = SIGROW.SERNUM9; // X-coordinate

  // Read I2C address
  eeprom_i2c_address = EEPROM.read(0);
  if ((eeprom_i2c_address > 119) || (eeprom_i2c_address <9)) eeprom_i2c_address=119; //set default and valid i2c address

  for (byte i = 0; i < NUMBER_OF_SCALE_READINGS_BUFFER; i++)
    last_scale_raw_readings[i] = 0;

  sw.setTxBuffer(swTxBuffer, sizeof(swTxBuffer));
  sw.setRxBuffer(swRxBuffer, sizeof(swRxBuffer));
  sw.setDelay_us(5);
  sw.setTimeout_ms(200);
  sw.begin();

  Serial.print("MAC address:");
  for (byte i = 0; i < 6; i++)
  {
    Serial.print(" 0x");
    Serial.print(device_mac_address[i], HEX);
  }
  Serial.println();
  Serial.print("I2C address: ");
  Serial.print(eeprom_i2c_address);
  Serial.print("(dec) 0x");
  Serial.print(eeprom_i2c_address, HEX);
  Serial.println("(hex)");

  Serial.print("Scale detected: ");
  if (myScale.begin(sw) == false)
  {
    Serial.println("NOT okay. ");
    // while (1); //Make the wathdog perform reset
  }
  else
  {
    Serial.println("okay");
  }

  ///**************************************
  Wire.swap(1); // Select the right pins

  // Initializing slave with secondary address
  // 1st argument: 1st address to listen to
  // 2nd argument: listen to general broadcast or "general call" (address 0x00)
  // 3rd argument: bits 7-1: second address if bit 0 is set true
  //               or bit mask of an address if bit 0 is set false
  Wire.begin(eeprom_i2c_address, true, WIRE_ALT_ADDRESS(8));

  // Handler für das I2C-Empfangsereignis festlegen (siehe unten)
  Wire.onReceive(receiveEvent);
  Wire.onRequest(requestHandler);

  pinMode(LED_BUILTIN, OUTPUT);
  digitalWrite(LED_BUILTIN, LOW); // Bord-LED

  answer_bit = false; // Do not answer to requests on I2C address 0x8
}

void loop()
{
  if (restart_at_next_possibility)
  {
    Wire.end();
    while (true)
      ;
    resetViaSWR();
  }
  if (update_i2c_address_from_eeprom)
  {
    eeprom_i2c_address = EEPROM.read(0);
    Wire.end();
    Serial.println("I2C end.");
    Wire.begin(eeprom_i2c_address, true, WIRE_ALT_ADDRESS(8));
    Serial.print("I2C mit neuer I2C Adresse ");
    Serial.print(eeprom_i2c_address);
    Serial.println(" gestartet.");
    update_i2c_address_from_eeprom = false;
  }

  if (register_select_readout == 2)
  { // Perform self test now!
    chip_test_perform();
  }

  if (myScale.available())
  {
    last_scale_raw_reading = myScale.getReading();

    // Fill ring buffer
    last_scale_raw_readings_ringbuffer_index++;
    if (last_scale_raw_readings_ringbuffer_index >= NUMBER_OF_SCALE_READINGS_BUFFER)
      last_scale_raw_readings_ringbuffer_index = 0;
    averaged_reading_sum -= last_scale_raw_readings[last_scale_raw_readings_ringbuffer_index];
    last_scale_raw_readings[last_scale_raw_readings_ringbuffer_index] = last_scale_raw_reading;
    averaged_reading_sum += last_scale_raw_reading;
    averaged_reading = averaged_reading_sum / NUMBER_OF_SCALE_READINGS_BUFFER;

    // Serial.print("Reading (avg): ");
    // Serial.println(averaged_reading);

    wdt_reset();
  }
}

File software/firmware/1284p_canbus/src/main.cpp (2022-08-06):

#include <Arduino.h>
#include <SPI.h>
#include <mcp2515.h>
#include <avr/wdt.h>
#include <EEPROM.h>
#include <OneWire.h>
#include <DallasTemperature.h>
#include <version.h>

// eink
#include <SPI.h>
#include "epd2in9_V2.h"
#include "epdpaint.h"
#include "imagedata.h"
#define COLORED 0
#define UNCOLORED 1

//scale hardware
#define SCALE_HARDWARE_REVISION 1

// NAU ADC
#include <Wire.h>
#include "SparkFun_Qwiic_Scale_NAU7802_Arduino_Library.h" // Click here to get the library: http://librarymanager/All#SparkFun_NAU7802

// CAN
struct can_frame canMsg;
MCP2515 mcp2515(4);       // CS connected to PIN 4
struct can_frame canMsg1; // To send messages

// OneWire
#define ONE_WIRE_BUS 23
#define TEMPERATURE_PRECISION 12
OneWire oneWire(ONE_WIRE_BUS);
DeviceAddress insideThermometer;
DallasTemperature sensors(&oneWire);
// function to print a device address
void printAddress(DeviceAddress deviceAddress)
{
  for (uint8_t i = 0; i < 8; i++)
  {
    if (deviceAddress[i] < 16)
      Serial.print("0");
    Serial.print(deviceAddress[i], HEX);
  }
}

// eink
unsigned char image[2048];
Paint paint(image, 0, 0); // width should be the multiple of 8
Epd epd;

// NAU
NAU7802 myScale;                                          // Create instance of the NAU7802 class
#define NUMBER_OF_SCALE_READINGS_BUFFER 8                 // should multiple of 2^N for fast division
long last_scale_raw_readings[NUMBER_OF_SCALE_READINGS_BUFFER];
byte last_scale_raw_readings_ringbuffer_index = 0; // points to the actual index used
long averaged_reading_sum = 0;                     // helper variable to average all entries in last_scale_raw_readings. needs to be divided by NUMBER_OF_SCALE_READINGS_BUFFER to get real average
long averaged_reading = 0;                         // regularly updated: averaged_reading_sum/NUMBER_OF_SCALE_READINGS_BUFFER

// Overall scale variables
uint16_t scale_device_id = 0;
char scale_product_description[50];
char scale_product_details_line1[50];
char scale_product_details_line2[50];
float scale_product_price_per_unit;
float scale_product_mass_per_unit;  // in kg
float scale_calibration_slope;      // in kg/au
long scale_calibration_zero_in_raw; // in raw arbitrary units of the adc

void read_scale_properties_from_EEPROM()
{
  EEPROM.get(10, scale_product_description);
  EEPROM.get(60, scale_product_details_line1);
  EEPROM.get(110, scale_product_details_line2);
  EEPROM.get(200, scale_product_price_per_unit);
  EEPROM.get(204, scale_product_mass_per_unit);   //@ CC
  EEPROM.get(208, scale_calibration_slope);       //@ D0
  EEPROM.get(212, scale_calibration_zero_in_raw); //@ D4
}
void write_scale_properties_to_EEPROM()
{
  EEPROM.put(10, scale_product_description);    //@ 0a
  EEPROM.put(60, scale_product_details_line1);  //@ 3c
  EEPROM.put(110, scale_product_details_line2); //@ 6e
  EEPROM.put(200, scale_product_price_per_unit);
  EEPROM.put(204, scale_product_mass_per_unit);   //@ CC
  EEPROM.put(208, scale_calibration_slope);       //@ D0
  EEPROM.put(212, scale_calibration_zero_in_raw); //@ D4
}

void setup()
{
  for (byte i = 0; i < NUMBER_OF_SCALE_READINGS_BUFFER; i++)
    last_scale_raw_readings[i] = 0;
  pinMode(LED_BUILTIN, OUTPUT);

  Serial.begin(115200);

  // OneWire start
  //  Start up the library
  sensors.begin();
  Serial.print("Locating OneWire devices...");
  Serial.print("Found ");
  Serial.print(sensors.getDeviceCount(), DEC);
  Serial.println(" devices.");
  // report parasite power requirements
  Serial.print("Parasite power is: ");
  if (sensors.isParasitePowerMode())
    Serial.println("ON");
  else
    Serial.println("OFF");

  // method 1: by index
  if (!sensors.getAddress(insideThermometer, 0))
    Serial.println("Unable to find address for Device 0");
  // show the addresses we found on the bus
  Serial.print("Device 0 Address: ");
  printAddress(insideThermometer);
  Serial.println();

  sensors.setResolution(insideThermometer, TEMPERATURE_PRECISION);
  Serial.print("Device 0 Resolution: ");
  Serial.print(sensors.getResolution(insideThermometer), DEC);
  Serial.println();

  sensors.setWaitForConversion(false); // make sensors.requestTemperatures calls async
  // OneWire end

  // NAU start
  Wire.begin();

  if (myScale.begin() == false)
  {
    Serial.println("Scale not detected. Please check wiring. Freezing...");
  }
  Serial.println("Scale detected!");
  // NAU end

  // Set scale_device_id start
  // eg OneWire ROM = 28 6D 1A 2 D 0 0 41
  //-->  scale_device_id = 1A<<8 + 6d
  scale_device_id = insideThermometer[1] + (insideThermometer[2] << 8);
  Serial.print("scale_device_id (according to OneWire address): 0x");
  Serial.println(scale_device_id, HEX);
  // store this in eeprom 0 and 1 of not set already
  uint16_t scale_device_id_read;
  EEPROM.get(0, scale_device_id_read);
  if (scale_device_id_read != scale_device_id)
  {
    Serial.print("scale_device_id in EEPROM at byte 0 and 1 reads: 0x");
    Serial.println(scale_device_id_read, HEX);
    EEPROM.put(0, scale_device_id);
    Serial.println("scale_device_id in EEPROM corrected.");
  }
  // Set scale_device_id end

  // CAN start
  mcp2515.reset();
  mcp2515.setBitrate(CAN_125KBPS, MCP_8MHZ);
  mcp2515.setNormalMode();
  // Send actual Firmware version
  canMsg1.can_id = (0x00020000 + scale_device_id) | CAN_EFF_FLAG;
  canMsg1.can_dlc = 5;
  canMsg1.data[0] = BUILD_NUMBER & 0xff;         // build lsb
  canMsg1.data[1] = (BUILD_NUMBER >> 8) & 0xff;  //
  canMsg1.data[2] = (BUILD_NUMBER >> 16) & 0xff; //
  canMsg1.data[3] = (BUILD_NUMBER >> 24) & 0xff; // build msb
  canMsg1.data[4] = SCALE_HARDWARE_REVISION & 0xff; // scale hardware revision
  mcp2515.sendMessage(&canMsg1);

  Serial.println("------- CAN Read ----------");
  Serial.println("ID  DLC   DATA");

  // Set CAN Filters
  // see page 34 in MCP2515 Manual
  // https://ww1.microchip.com/downloads/en/DeviceDoc/MCP2515-Stand-Alone-CAN-Controller-with-SPI-20001801J.pdf
  // Further hint from Arduino forum:
  //    To avoid errors you need to set all masks and filters (otherwise it can be rubbish there)
  mcp2515.setConfigMode();
  mcp2515.setFilterMask(MCP2515::MASK0, true, 0x0000ffff); // Look only for device_id
  mcp2515.setFilter(MCP2515::RXF0, true, scale_device_id);
  mcp2515.setFilterMask(MCP2515::MASK1, true, 0x10000000); // and broadcast meassages
  mcp2515.setFilter(MCP2515::RXF1, true,      0x10000000);
  mcp2515.setNormalMode();
  // CAN end

  // EEPROM start
  Serial.print("eeprom: ");
  for (byte i = 0; i < 200; i++)
  {
    Serial.print(EEPROM.read(i));
    Serial.print(" ");
  }
  Serial.println();

  read_scale_properties_from_EEPROM();
  // EEPROM end

  // eink start
  // For version 2 displays, the following complete init seems to be necessary:
  // 1st clear twice the full screen
  // 2nd call SetFrameMemory_Base() with an image
  // 3rd now call "_partical" commands
  if (epd.Init() != 0)
  {
    Serial.print("e-Paper init failed");
  }
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

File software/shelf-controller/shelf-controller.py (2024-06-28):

#!/usr/bin/python3

import serial
import time
import re
import struct
import logging, argparse
import json
import paho.mqtt.client as paho
import queue, traceback
import signal
import sys
import collections, statistics
import math
import socket
import os

logging.basicConfig(format="%(asctime)-15s %(levelname)-8s  %(message)s")
logger = logging.getLogger("Shelf Readout")

parser = argparse.ArgumentParser(description='Shelf Readout.')
parser.add_argument("-v", "--verbosity", help="increase output verbosity", default=0, action="count")
parser.add_argument("-b", "--mqtt-broker-host", help="MQTT broker hostname", default="localhost")
parser.add_argument("serial_device_name", help="eg /dev/ttyUSB0", type=str)
args = parser.parse_args()
logger.setLevel(logging.WARNING-(args.verbosity*10 if args.verbosity <=2 else 20) )

debug = True if args.verbosity>1 else False



#######################################################################

def send_and_recv(str_to_send, echo_out = False, print_return = False):
    logger.debug(f"<<{str_to_send}")
    ser.write(str_to_send.encode() + b'\n')

    out = ser.readline().decode().strip()
    if out != '' and print_return:
        logger.debug(f">>{out}")

    # analyse output
    # Define the regular expression pattern to capture the relevant parts
    pattern = r'^([rw])\s+((?:[A-Fa-f0-9]{2}\s+){1,})$'

    # Use the regular expression to match the input string
    match = re.match(pattern, out+"\n")

    ret_val = []
    command = None
    if match:
        # Extract the captured groups
        command = match.group(1)     # 'r' or 'w'
        hex_numbers = match.group(2).split()   # Split numbers separated by spaces

        # Convert numbers to integers (base 16) and print the results
        #print(f"Command: {command}")
        #print("Hex Numbers:")
        for number in hex_numbers:
            decimal_number = int(number, 16)
            ret_val = ret_val + [decimal_number]
            #print(decimal_number)
    else:
        logger.warning(f"Invalid data from serial: {out=} when sending {str_to_send=}")

    return (command, ret_val)


def bin_search():
    # MAC addresses scan range
    min = 0x0
    max = 0xffff_ffff_ffff

    l = min
    r = max
    i = 0
    while i<52:
        m = l + (r-l)//2

        #print(f"i: {i} {l:014_X} {m:014_X} {r:014_X}")
        str_to_send = f"w0003{m:#014X}".replace("0X","")
        #print(str_to_send)
        send_and_recv(str_to_send)

        str_to_send = f"r0801"
        #print(str_to_send)

        res = send_and_recv(str_to_send)
        #print(res)

        if res[1][1] == 0x00:
            if r-l<=1: return m #Ausgabe, falls 0 gesucht wurde
            r = m
        else:
            if r-l<=1: return r #Ausgabe aller anderen Adressen
            l = m+1

        i+=1

    return False #nichts gefunden. Waage während des Suchlaufs kaputtgegangen?

#get usb path of device
usb_path_device = "unknown"
last_dev = os.popen(f'udevadm info /{args.serial_device_name} | grep DEVLINKS').read()
regex = r"-usb-[0-9:\.]+-port0"
matches = re.finditer(regex, last_dev, re.MULTILINE)
for matchnum, match in enumerate(matches): #only one match should be found
    s=match.group()
    usb_path_device = s.replace(":","-").replace("-usb-","").replace("-port0","")
mqtt_client_name = f"scale-{socket.gethostname()}-{usb_path_device}"
#mqtt_client_name = f"scale-{socket.gethostname()}-{args.serial_device_name.replace('/','-')}"

logger.info(f"This is the MQTT-Client-ID: {mqtt_client_name}")
#######################################################################
# MQTT functions
def on_connect(client, userdata, flags, rc):
    if rc==0:
        logger.info("MQTT connected OK. Return code "+str(rc) )
        client.subscribe("homie/"+mqtt_client_name+"/cmd/#")
        client.subscribe(f"homie/{mqtt_client_name}/cmd/scales/+/led")
        client.subscribe("homie/shop_controller/shop_status")
        logger.info("MQTT: Success, subscribed to all topics")

        client.publish(f"homie/{mqtt_client_name}/state", '1', qos=1, retain=True)

    else:
        logger.error("Bad connection. Return code="+str(rc))

def on_disconnect(client, userdata, rc):
    if rc != 0:
        logger.warning("Unexpected MQTT disconnection. Will auto-reconnect")

mqtt_queue=queue.Queue()
def on_message(client, userdata, message):
    global mqtt_queue
    try:
        mqtt_queue.put(message)
        m = message.payload.decode("utf-8")
        logger.debug("MQTT message received. Topic: "+message.topic+" Payload: "+m)
    except Exception as err:
        traceback.print_tb(err.__traceback__)


#connect to MQTT broker
client = paho.Client(paho.CallbackAPIVersion.VERSION1, mqtt_client_name)
client.on_message=on_message
client.on_connect = on_connect
client.on_disconnect = on_disconnect
client.enable_logger(logger) #info: https://www.eclipse.org/paho/clients/python/docs/#callbacks
logger.info("connecting to broker: "+args.mqtt_broker_host+". If it fails, check whether the broker is reachable. Check the -b option.")

# start with MQTT connection and set last will
logger.info(f"mqtt_client_name: {mqtt_client_name}")
client.will_set(f"homie/{mqtt_client_name}/state", '0', qos=1, retain=True)
client.connect(args.mqtt_broker_host)
client.loop_start() #start loop to process received messages in separate thread
logger.debug("MQTT loop started.")

##############################################################################

#Global information on all scales
anzahl_waagen = 0
waagen = {} #index: i2c_add   eg: 9: {'mac': "493037D20E1B", 'address': 9, 'slope': 1, 'zero':0, 'state': 0, ...},}
LUT_MAC_2_I2C_ADD = {} #LUT to get I2C address from MAC address
shop_status = 0

##############################################################################
main_loop_var = True
def signal_handler(sig, frame):
    global main_loop_var
    logger.info(f"Program terminating. Sending correct /state for all {anzahl_waagen} scales... (this takes 1 second)")

    main_loop_var = False
#    sys.exit(0)

signal.signal(signal.SIGINT, signal_handler)
signal.signal(signal.SIGTERM, signal_handler)
##############################################################################


ser = serial.Serial(port=args.serial_device_name, baudrate=115200, timeout=1 )
#ser.isOpen()

# Waagen Neustart
send_and_recv("w0000")
logger.info("Warte auf Waagen, bis sie den Neustart ausgeführt haben. 8 Sekunden ...")
time.sleep(8)

##alle LEDs an
send_and_recv("w0005")
time.sleep(0.9)
#Antwort bit setzen
send_and_recv("w0001")
time.sleep(.1)
#alle LEDs aus
send_and_recv("w0004")
time.sleep(.1)
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

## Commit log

2019-10-18 Design der Anzeige verbessern.
2019-11-09 Anzeige von Produkt-Typ und Beschreibung + MQTT Name
2019-12-13 Verwaltung hinzugefügt
    [Analyse 200g.xlsx, Analyse Linearität.xlsx, Waage März 2019.xlsx]
2019-12-15 Änderungen an Einfacher Waage
    Andere Befestigungsweise der Wägezellen an Grundplatte
    Mit zwei M3 Schrauben in gleicher Achse mit Auflastpunkt
    Vorteile:
    - 4x weniger M3 Gewinde in Grundplatte -> weniger Herstellungskosten
    - Keine Bohrung der Wägezellen nötig.
2020-10-29 working prototype
2020-11-02 Breite der Fräsung für Trenner: 2.0mm
    Kleine Änderung bei der Breite der Einfräsung für Trenner: Jetzt 2.0mm anstatt zuvor 2.1mm. Durch das Werkzeug allein wird später der 2.0mm breite Trenner gut passen.
2022-02-19 new schematic and pcb
    [1284pTest2.kicad_pcb, 1284pTest2.kicad_sch, Analyse 200g.xlsx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]
2022-02-20 fues added and small movements
    [1284pTest2.kicad_pcb, 1284pTest2.kicad_sch, power.kicad_sch]
2022-02-23 CAN SPI CS pin corrected and PCB optimisations.
    [1284pTest2.kicad_pcb, 1284pTest2.kicad_sch, controller.kicad_sch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]
2022-02-25 interactive HTML-BOM added
2022-03-06 second LDO for eink added
    [1284pTest2.kicad_pcb, 1284pTest2.kicad_sch, eink.kicad_sch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]
2022-03-07 JP1 added
    [1284pTest2.kicad_pcb, 1284pTest2.kicad_sch, eink.kicad_sch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]
2022-03-13 Error on JP1 fixed and changed scale wires pads
    [1284pTest2.kicad_pcb, 1284pTest2.kicad_sch, CAN.kicad_sch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]
2022-03-23 bus terminator and shelf controller added
    [1284pTest2.kicad_pcb, 1284pTest2.kicad_sch, bus terminator.kicad_pcb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]
2022-03-23 1st complete working version with 1284p and canbus
2022-03-27 ADC averaging with ring buffer added
2022-07-10 40pol connector rotated and other small mods.
    [regal-controller.kicad_pcb, regal-controller.kicad_sch]
2022-10-23 Update ablauf.md
    Änderungen mit Distanzsensoren und OHNE Bestätigungsmodul im Laden.
2022-10-24 Update ablauf.md
    Unter Berücksichtigung, dass die Distanzsensoren nicht immer alle Personen im Raum abdecken. Außerdem kann die Tür die Sensoren negativ beeinflussen.
2022-10-24 Logik anpassungen und mehr
2022-10-30 small error corrections for shop-control and more small fixes
    [shelf-controller.py]
2022-10-31 Update ablauf.md
    - [ ] Neuer Zustand vor dem Öffnen des Ladens: Vorbereiten der Wagen, dann erst betreten
    - [ ] Neuer Zustand einfügen vor 5: Warenkorb wird übermittelt für die Rechnung
2022-10-31 First version display-power-control added
2022-10-31 improvements to display-power-control
2022-10-31 Display power switches added to nodered
2022-11-24 shop-control switches light via Generic_PIR
2022-11-24 upload.sh now switches light
2022-11-27 added 2nd camera for upload.
2023-01-29 Waage mit Schalter UND Distance-Sensor hinzugefügt
    [Untitled.kicad_pcb, Untitled.kicad_sch, Untitled.step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]
2023-01-29 clean up
    [Untitled 2.kicad_pcb, Untitled 2.kicad_sch, Untitled 2.step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]
2023-01-29 cleanup part 2
    [Untitled 2.kicad_pcb, Untitled 2.kicad_sch, Untitled 2.step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]
2023-01-29 moved older version to corresponding directories
    [1284pTest2.kicad_pcb, 1284pTest2.kicad_sch, Analyse 200g.xlsx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]
2023-03-15 actual status Waage V4 added
    [Untitled.kicad_pcb, Untitled.kicad_sch, Untitled.step]
2023-04-12 intermediate step
    [Untitled.kicad_pcb, Untitled.kicad_sch, Untitled.step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]
2023-04-14 Zwischenstand Elektronik v4
    [Untitled.kicad_pcb, Untitled.kicad_sch, Untitled.step]
2023-04-25 small updates to PCB design
    [Untitled.kicad_pcb, Untitled.step]
2023-06-14 added basic construct for lidar
2023-06-24 lidar readout
2023-07-25 I2C Zwischenstand
2023-07-26 intermediate i2c updates
2023-11-07 Datein für die Produktion
    [Untitled.csv, Untitled.kicad_sch, bom.csv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]
2023-11-07 shelf controller USB added
    [SM04B-SRSS-TB(LF)(SN)--3DModel-STEP-56544.STEP, SM04B-SRSS-TB_LF__SN_.step, bom.csv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]
2023-11-11 cleanup of old data
    [Waage März 2019.xlsx]
2023-12-24 shop-track-collector added
2023-12-30 Make shop-track-collector work
2023-12-31 Bug fix for setting I2C address
    [main.cpp]
2024-01-16 Aufräumen
    [1284pTest2.kicad_pcb, 1284pTest2.kicad_sch, Analyse 200g.xlsx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]
2024-01-18 Erste Schritte für die automatische Installation von RaspiOS
2024-03-29 correct TOF 4x4 heatmap
2024-03-30 service file for display power control without debug
2024-04-02 shop-track mqtt name extended
2024-04-04 display-power-control for Wayland
2024-04-07 bug fix for calculation of average
    [shop-track.py]
2024-04-07 bug fix for min std-deviation
    [shelf-controller.py]
2024-04-11 Anpassung der Readme
2024-04-11 Öffnung des Ladens für Testkäufer via Remote MQTT-Broker, Bug fix für Summenberechnung falls Produkt auf mehreren Waagen, Artikelpflege via Nodered
2024-04-19 Sync der DB und Zugriff für Lieferanten
2024-04-19 Rechnungen anzeigen und Sync zur remote DB
2024-04-27 TTS unterstützen und kleine Verbesserungen
2024-05-06 bug fix und tipps aufgenommen
2024-05-18 PCB drawings added
2024-05-20 tof-camera added service and install.sj
2024-05-20 tof-camera set_zero on shop-status
2024-05-20 tof-camera in shop-control eingebaut.
2024-05-21 Warenkorb aus der Ferne bearbeiten, HTML Seite
2024-06-15 added state to shop-track
2024-06-15 state for track-collector and msg rate limit
2024-06-15 Fix: send /state in onConnect
    [io-usb-readout.py, shelf-controller.py, shop-track.py]
2024-06-15 state for tof camera
2024-06-22 eink pico firmware first attempt
    [myconfig_assigned_scale.txt]
2024-06-23 working eink firmware
    [myconfig_assigned_scale.txt]
2024-06-28 Bugfixes und Anpassungen:
    timeouts angepasst, damit bei längerer Nutzung des Kartenterminals es zu keinem technischen Fehler des Ladens kommt. Außerdem soll man die Türe auch bei Zustand 8 öffnen können.
    Wenn es zu einem Lesefehler bei einer Waage kommt, soll nicht gleich das ganze Skript abstürzen.
    sync_to_mysql.py jetzt mit sync-bit
    Filter bei mqtt-2-ntfy auf interessante Dinge um nicht ins Limit zu laufen.
    [shelf-controller.py]

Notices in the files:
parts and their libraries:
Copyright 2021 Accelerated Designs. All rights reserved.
